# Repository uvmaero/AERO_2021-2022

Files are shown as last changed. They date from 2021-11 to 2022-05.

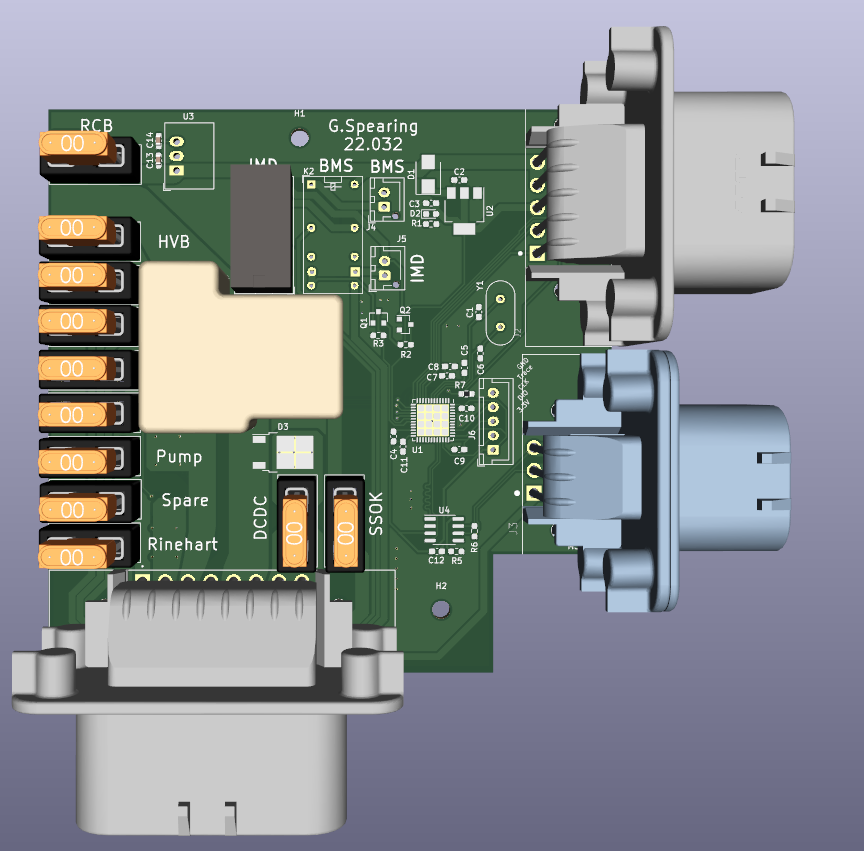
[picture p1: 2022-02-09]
Board_Images/RCB_3d_front.png

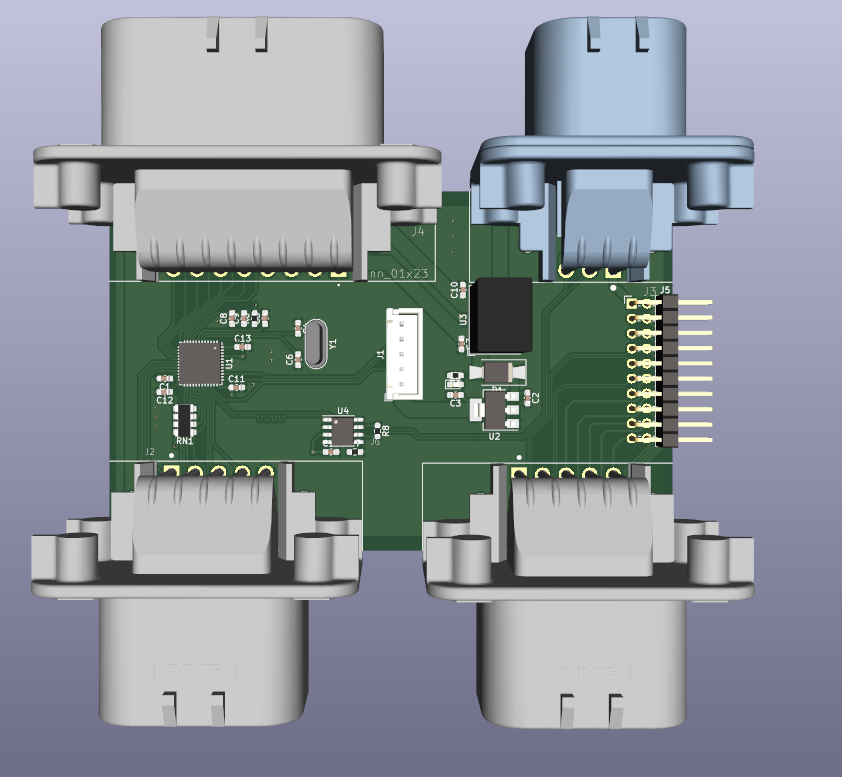
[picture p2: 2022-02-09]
Board_Images/DCB_3d_front.png

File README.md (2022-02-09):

# AERO_2021-2022

AERO Code and PCBs for CleanSpeed 5.0

This is all the boards and code we generate

## File Structure
Files here are for both the PCB and the firmware. 

{Board_Name}/{Board_Name_Firmware} -> holds the files for the firmware

{Board_Name}/{Board_Name_PCB} -> holds the KiCad files for the PCB

## Board Information

 - BCP: BMS Connector Pass through
 - DCB: Driver Contorl Board
 - HVB: High Voltage Board
 - MRP: Motor Resolver Passthrough
 - RCB: Rear Control Board

To read more about the boards go to [Board Descriptions](Board_Descriptions.md)

## Code Information

Code descrpitions can be found in [Firmware Descriptions](Firmware_Descriptions.md)

## Wireless Transceiver Information

There's also a wireless project. More information to come.

## Willem Review Notes: 

@Willem -> put any notes you have regarding boards here. 
Please review RCB, DCB, HVB, PAM

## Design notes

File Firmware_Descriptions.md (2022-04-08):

# Firmware Descrptions

Here you'll find more information about the firmware of each of the boards throughout the car. You can expect to find documentation for things like each function used, a program flow chart, CAN addresses and message content, and more. 

## Diver Control Board
### Overview: 
This board controls all of the hardware that the driver needs to interface with to drive the car, as well as gathers sensor data from the forward sensors. For the driver, this board manages the LCD heads up display and each of the controls that modifies the way the car drives. The coast regeneration and brake regeneration knobs, start button, accelerate and brake pedals all send their data to the Driver Control Board. The HUD that provides information to the driver about the is driven by this board as well. Like all boards on the car, this board communicates with the rest of the vehicle using the CAN protocol. 
### Flowchart:

### Function Definitons:
#### pollSensorData:
Input Parameters: void  
Return Type & Value: void  
Description: Reads each sensor that the board monitors and updates the appropriate global variable holding the sensor value.  
### HAL_GPIO_EXTI_Callback
Input Parameters: uint16_t GPIO_PIN
Return Type & Value: void
Description: The IRQ handler for the start button, this will send a ready to drive CAN message to rinehart, enabling the car to drive!

### accel_pedal_compare
Input Parameters: uint8_t pedal0, uint8_t pedal1
Return Type & Value: uint8_t pedal_average (the average pedal value computed)
Description: compares the two samples from the pedal potentiometeres to ensure that the values are within 10 millivolts of eachother to prevent unintended acceleration (very dangerous!)

### CAN Information: 
#### Outgoing Messages:
Front Left Wheel Speed: int 0 - 255 (rpm)  
Front Right Wheel Speed: int 0 - 255  
Front Right Suspension: int 0 - 255 (spring depression scaled to 0 - 255)  
Front Left Suspension: int 0 - 255 (spring depression scaled to 0 - 255)  
Brake 1: 
Brake 2: 
Pedal 1: 
Pedal 2: 

#### Incoming Messages:
Rear Left Wheel Speed: Rear Control Board - int 0 - 255 (rpm)  
Rear Right Wheel Speed: Rear Control Board - int 0 - 255 (rpm)  
Rear Right Suspension: Rear Control Board - int 0 - 255 (spring depression scaled to 0 - 255)  
Rear Left Suspension: Rear Control Board - int 0 - 255 (spring depression scaled to 0 - 255)  
Read to Drive State: High Voltage Board - int 0 or 1 

#### Addresses:
0x90: Base - [0x00, 0x01, 0x02, 0x03, 0x04, 0x05, 0x06, 0x07]  
0x91: Prog - [Torque Setting, 0x01, 0x02, 0x03, 0x04, 0x05, 0x06, 0x07]  
0x92: DAQ-DATA - [Left Wheel Speed, Right Wheel Speed, Left Suspension, Right Suspension, Brake 1, Brake 2, Pedal 1, Pedal 2]    
0x93: CONTROL DATA - [Brake Regen, Coast Regen, Cooling, Drive Direction, 0x04, 0x05, 0x06, 0x07]  

## Rear Control Board
### Overview: 
### Flowchart:

### Function Definitons:
#### pollSensorData:
Input Parameters: void  
Return Type & Value: void  
Description: Reads each sensor that the board monitors and updates the appropriate global variable holding the sensor value.

### CAN Information: 

#### Outgoing Messages:
Rear Left Wheel Speed: int 0 - 255 (rpm)  
Rear Right Wheel Speed: int 0 - 255  
Rear Right Suspension: int 0 - 255 (spring depression scaled to 0 - 255)  
Rear Left Suspension: int 0 - 255 (spring depression scaled to 0 - 255)  

#### Incoming Messages:
Brake Light State: Dash Control Board - int 0 or 1
Fan State: Dash Control Board - int 0 or 1

#### Addresses:
0x80: Base - [0x00, 0x01, 0x02, 0x03, 0x04, 0x05, 0x06, 0x07]  
0x81: DAQ DATA - [Left Wheel Speed, Right Wheel Speed, Left Suspension, Right Suspension, Water Temperature Inlet, Water Temperature Outlet, 0x06, 0x07]  
0x82: CONTROL DATA - [Brake Signal, Pump Signal, Fan Signal, 0x04, 0x05, 0x06, 0x07]  

## High Voltage Board
### Overview: 
### Flowchart:

### Function Definitons:
#### pollSensorData:
Input Parameters: void  
Return Type & Value: void  
Description: Reads each sensor that the board monitors and updates the appropriate global variable holding the sensor value.

### CAN Information:

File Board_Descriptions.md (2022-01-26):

# Board Descirptions

This file will list the boards and where to find more information about them. 

## Diver Control Board

## Driver Interface Board

## Rear Control Board

## High Voltage Board

## Pack Manager Board

## Emrax Resolver Board

## BMS Pass Through Board

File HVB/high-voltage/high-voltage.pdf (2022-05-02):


12/04/2022

high-voltage Project
Configuration Report

## 1. Description

### 1.1. Project

Project Name | high-voltage
Board Name | custom
Generated with: | STM32CubeMX 6.4.0
Date | 04/12/2022

### 1.2. MCU

MCU Series | STM32F4
MCU Line | STM32F413/423
MCU name | STM32F413CGUx
MCU Package | UFQFPN48
MCU Pin number | 48

### 1.3. Core(s) information

Core(s) | Arm Cortex-M4

## 2. Pinout Configuration

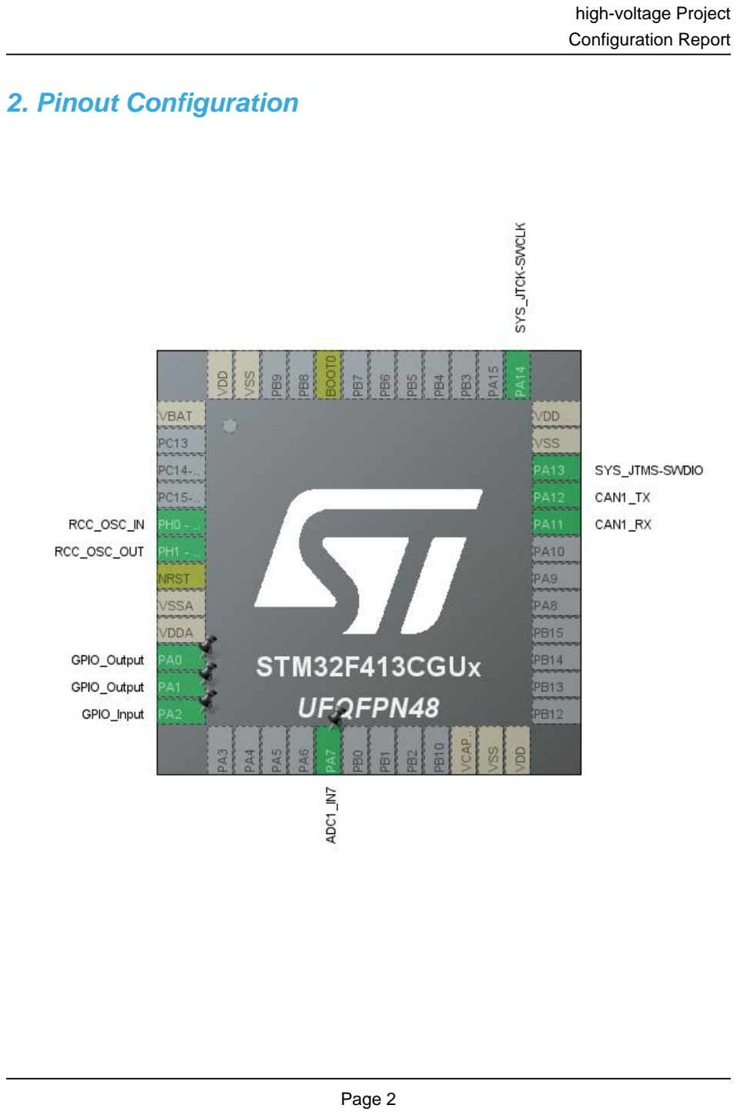
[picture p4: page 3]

## 3. Pins Configuration

Pin Number UFQFPN48 | Pin Name (function after reset) | Pin Type | Alternate Function(s) | Label
1 | VBAT | Power
5 | PH0 - OSC_IN | I/O | RCC_OSC_IN
6 | PH1 - OSC_OUT | I/O | RCC_OSC_OUT
7 | NRST | Reset
8 | VSSA | Power
9 | VDDA | Power
10 | PA0 * | I/O | GPIO_Output
11 | PA1 * | I/O | GPIO_Output
12 | PA2 * | I/O | GPIO_Input
17 | PA7 | I/O | ADC1_IN7
22 | VCAP_1 | Power
23 | VSS | Power
24 | VDD | Power
32 | PA11 | I/O | CAN1_RX
33 | PA12 | I/O | CAN1_TX
34 | PA13 | I/O | SYS_JTMS-SWDIO
35 | VSS | Power
36 | VDD | Power
37 | PA14 | I/O | SYS_JTCK-SWCLK
44 | BOOT0 | Boot
47 | VSS | Power
48 | VDD | Power

* The pin is affected with an I/O function

## 4. Clock Tree Configuration

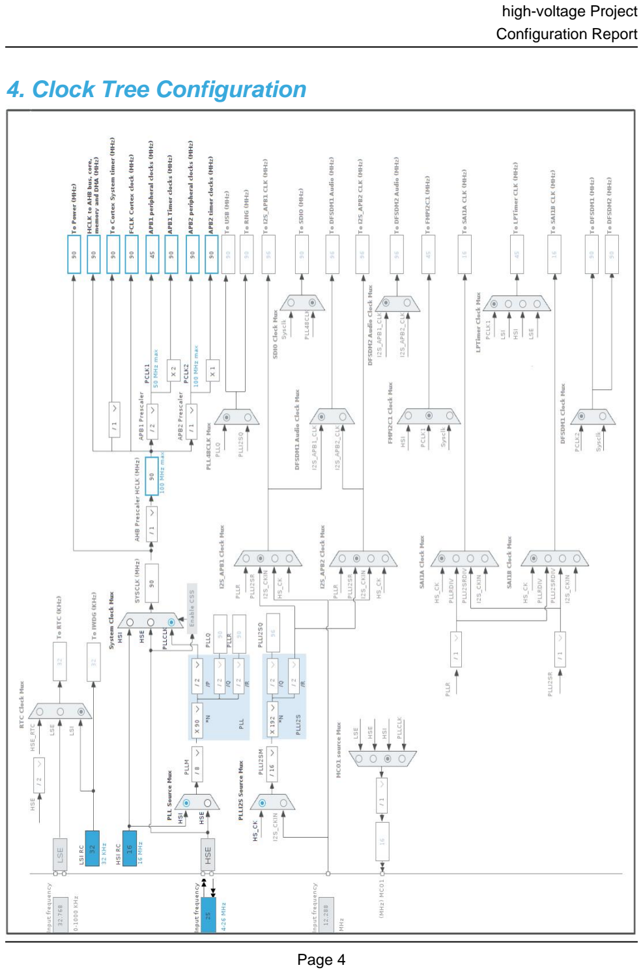
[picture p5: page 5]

## 5. Software Project

### 5.1. Project Settings

Name | Value
Project Name | high-voltage
Project Folder | /home/george/Documents/GitHub/AERO/AERO_2021-2022/HVB/high-voltage
Toolchain / IDE | Makefile
Firmware Package Name and Version | STM32Cube FW_F4 V1.26.2
Application Structure | Advanced
Generate Under Root | No
Do not generate the main() | No
Minimum Heap Size | 0x200
Minimum Stack Size | 0x400

### 5.2. Code Generation Settings

Name | Value
STM32Cube MCU packages and embedded software | Copy only the necessary library files
Generate peripheral initialization as a pair of '.c/.h' files | No
Backup previously generated files when re-generating | No
Keep User Code when re-generating | Yes
Delete previously generated files when not re-generated | Yes
Set all free pins as analog (to optimize the power consumption) | No
Enable Full Assert | No

### 5.3. Advanced Settings - Generated Function Calls

Rank | Function Name | Peripheral Instance Name
1 | MX_GPIO_Init | GPIO
2 | SystemClock_Config | RCC
3 | MX_CAN1_Init | CAN1
4 | MX_DMA_Init | DMA
5 | MX_ADC1_Init | ADC1
6 | MX_TIM14_Init | TIM14
7 | MX_TIM13_Init | TIM13

## 6. Power Consumption Calculator report

### 6.1. Microcontroller Selection

Series | STM32F4
Line | STM32F413/423
MCU | STM32F413CGUx
Datasheet | DS11581_Rev5

### 6.2. Parameter Selection

Temperature | 25
Vdd | 1.7

### 6.3. Battery Selection

Battery | Li-SOCL2(A3400)
Capacity | 3400.0 mAh
Self Discharge | 0.08 %/month
Nominal Voltage | 3.6 V
Max Cont Current | 100.0 mA
Max Pulse Current | 200.0 mA
Cells in series | 1
Cells in parallel | 1

### 6.4. Sequence

Step | Step1 | Step2
Mode | RUN | STOP
Vdd | 1.7 | 1.7
Voltage Source | Battery | Battery
Range | Scale1-High | No Scale
Fetch Type | FLASH/ART/PREFETCH | n/a
CPU Frequency | 100 MHz | 0 Hz
Clock Configuration | HSE PLL | Regulator_LPLV Flash-PwrDwn
Clock Source Frequency | 4 MHz | 0 Hz
Peripherals
Additional Cons. | 0 mA | 0 mA
Average Current | 25.4 mA | 15.3 µA
Duration | 0.1 ms | 0.9 ms
DMIPS | 125.0 | 0.0
Ta Max | 103.62 | 105
Category | In DS Table | In DS Table

### 6.5. Results

Sequence Time | 1 ms | Average Current | 2.55 mA
Battery Life | 1 month, 24 days, 23 hours | Average DMIPS | 125.0 DMIPS

### 6.6. Chart

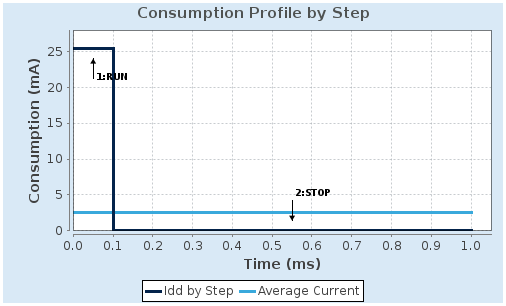
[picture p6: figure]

## 7. Peripherals and Middlewares Configuration

### 7.1. ADC1

mode: IN7
7.1.1. Parameter Settings:

ADCs_Common_Settings:

Mode | Independent mode
ADC_Settings:
Clock Prescaler | PCLK2 divided by 4
Resolution | 12 bits (15 ADC Clock cycles)
Data Alignment | Right alignment
Scan Conversion Mode | Disabled
Continuous Conversion Mode | Enabled *
Discontinuous Conversion Mode | Disabled
DMA Continuous Requests | Enabled *
End Of Conversion Selection | EOC flag at the end of single channel conversion
ADC_Regular_ConversionMode:
Number Of Conversion | 1
External Trigger Conversion Source | Regular Conversion launched by software
External Trigger Conversion Edge | None
Rank | 1
Channel | Channel 7
Sampling Time | 3 Cycles
ADC_Injected_ConversionMode:
Number Of Conversions | 0
WatchDog:
Enable Analog WatchDog Mode | false

### 7.2. CAN1

mode: Activated
7.2.1. Parameter Settings:

Bit Timings Parameters:

Prescaler (for Time Quantum) | 6 *
Time Quantum | 133.33333333333331 *
Time Quanta in Bit Segment 1 | 12 Times *
Time Quanta in Bit Segment 2 | 2 Times *

Time for one Bit | 1999 *
Baud Rate | 500000 *
ReSynchronization Jump Width | 1 Time
Basic Parameters:
Time Triggered Communication Mode | Disable
Automatic Bus-Off Management | Enable *
Automatic Wake-Up Mode | Enable *
Automatic Retransmission | Enable *
Receive Fifo Locked Mode | Disable
Transmit Fifo Priority | Disable
Advanced Parameters:
Operating Mode | Normal

### 7.3. RCC

High Speed Clock (HSE): Crystal/Ceramic Resonator
7.3.1. Parameter Settings:

System Parameters:

VDD voltage (V) | 3.3
Instruction Cache | Enabled
Prefetch Buffer | Enabled
Data Cache | Enabled
Flash Latency(WS) | 3 WS (4 CPU cycle)
RCC Parameters:
HSI Calibration Value | 16
TIM Prescaler Selection | Disabled
HSE Startup Timout Value (ms) | 100
LSE Startup Timout Value (ms) | 5000
Power Parameters:
Power Regulator Voltage Scale | Power Regulator Voltage Scale 1

### 7.4. SYS

Debug: Serial Wire
Timebase Source: SysTick

### 7.5. TIM13

mode: Activated
7.5.1. Parameter Settings:

Counter Settings:

Prescaler (PSC - 16 bits value) | 9000-1 *
Counter Mode | Up
Counter Period (AutoReload Register - 16 bits value ) | 1000-1 *
Internal Clock Division (CKD) | No Division
auto-reload preload | Disable

### 7.6. TIM14

mode: Activated
7.6.1. Parameter Settings:

Counter Settings:

Prescaler (PSC - 16 bits value) | 9000-1 *
Counter Mode | Up
Counter Period (AutoReload Register - 16 bits value ) | 5000-1 *
Internal Clock Division (CKD) | No Division
auto-reload preload | Disable

* User modified value

## 8. System Configuration

### 8.1. GPIO configuration

IP | Pin | Signal | GPIO mode | GPIO pull/up pull down | Max Speed | User Label
ADC1 | PA7 | ADC1_IN7 | Analog mode | No pull-up and no pull-down | n/a
CAN1 | PA11 | CAN1_RX | Alternate Function Push Pull | No pull-up and no pull-down | High *
| PA12 | CAN1_TX | Alternate Function Push Pull | No pull-up and no pull-down | High *
RCC | PH0 -OSC_IN | RCC_OSC_IN | n/a | n/a | n/a
| PH1 -OSC_OUT | RCC_OSC_OUT | n/a | n/a | n/a
SYS | PA13 | SYS_JTMS-SWDIO | n/a | n/a | n/a
| PA14 | SYS_JTCK-SWCLK | n/a | n/a | n/a
GPIO | PA0 | GPIO_Output | Output Push Pull | Pull-down * | Low
| PA1 | GPIO_Output | Output Push Pull | Pull-up * | Low
| PA2 | GPIO_Input | Input mode | No pull-up and no pull-down | n/a

### 8.2. DMA configuration

DMA request | Stream | Direction | Priority
ADC1 | DMA2_Stream0 | Peripheral To Memory | Low

ADC1: DMA2_Stream0 DMA request Settings:

Mode: | Circular *
Use fifo: | Disable
Peripheral Increment: | Disable
Memory Increment: | Enable *
Peripheral Data Width: | Half Word
Memory Data Width: | Half Word

### 8.3. NVIC configuration

8.3.1. NVIC
Interrupt Table | Enable | Preenmption Priority | SubPriority
Non maskable interrupt | true | 0 | 0
Hard fault interrupt | true | 0 | 0
Memory management fault | true | 0 | 0
Pre-fetch fault, memory access fault | true | 0 | 0
Undefined instruction or illegal state | true | 0 | 0
System service call via SWI instruction | true | 0 | 0
Debug monitor | true | 0 | 0
Pendable request for system service | true | 0 | 0
System tick timer | true | 15 | 0
CAN1 RX0 interrupts | true | 0 | 0
TIM8 update interrupt and TIM13 global interrupt | true | 0 | 0
TIM8 trigger and commutation interrupts and TIM14 global interrupt | true | 0 | 0
DMA2 stream0 global interrupt | true | 0 | 0
PVD interrupt through EXTI line 16 | | unused
Flash global interrupt | | unused
RCC global interrupt | | unused
ADC1 global interrupt | | unused
CAN1 TX interrupts | | unused
CAN1 RX1 interrupt | | unused
CAN1 SCE interrupt | | unused
FPU global interrupt | | unused
8.3.2. NVIC Code generation

Enabled interrupt Table Select for init
sequence ordering
| | Generate IRQ
| | handler | Call HAL handler
Non maskable interrupt | false | true | false
Hard fault interrupt | false | true | false
Memory management fault | false | true | false
Pre-fetch fault, memory access fault | false | true | false
Undefined instruction or illegal state | false | true | false
System service call via SWI instruction | false | true | false
Debug monitor | false | true | false
Pendable request for system service | false | true | false
System tick timer | false | true | true
CAN1 RX0 interrupts | false | true | true

Enabled interrupt Table | Select for init sequence ordering | Generate IRQ handler | Call HAL handler
TIM8 update interrupt and TIM13 global interrupt | false | true | true
TIM8 trigger and commutation interrupts and TIM14 global interrupt | false | true | true
DMA2 stream0 global interrupt | false | true | true

* User modified value

## 9. System Views

9.1. Category view
9.1.1. Current

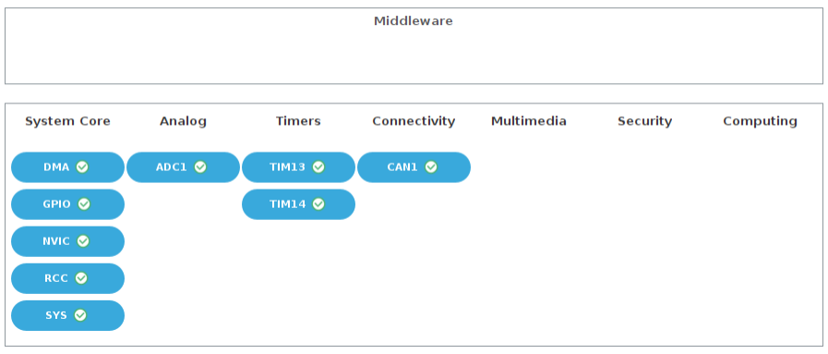
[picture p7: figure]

## 10. Docs & Resources

Type | Link
Datasheet | http://www.st.com/resource/en/datasheet/DM00282249.pdf
Reference manual | http://www.st.com/resource/en/reference_manual/DM00305666.pdf
Programming manual | http://www.st.com/resource/en/programming_manual/DM00046982.pdf
Errata sheet | http://www.st.com/resource/en/errata_sheet/DM00318678.pdf
Application note | http://www.st.com/resource/en/application_note/CD00167594.pdf
Application note | http://www.st.com/resource/en/application_note/CD00211314.pdf
Application note | http://www.st.com/resource/en/application_note/CD00249778.pdf
Application note | http://www.st.com/resource/en/application_note/CD00259245.pdf
Application note | http://www.st.com/resource/en/application_note/CD00264321.pdf
Application note | http://www.st.com/resource/en/application_note/CD00264342.pdf
Application note | http://www.st.com/resource/en/application_note/CD00264379.pdf
Application note | http://www.st.com/resource/en/application_note/DM00024853.pdf
Application note | http://www.st.com/resource/en/application_note/DM00040802.pdf
Application note | http://www.st.com/resource/en/application_note/DM00040808.pdf
Application note | http://www.st.com/resource/en/application_note/DM00042534.pdf
Application note | http://www.st.com/resource/en/application_note/DM00046011.pdf
Application note | http://www.st.com/resource/en/application_note/DM00072315.pdf
Application note | http://www.st.com/resource/en/application_note/DM00073742.pdf
Application note | http://www.st.com/resource/en/application_note/DM00073853.pdf
Application note | http://www.st.com/resource/en/application_note/DM00080497.pdf
Application note | http://www.st.com/resource/en/application_note/DM00081379.pdf
Application note | http://www.st.com/resource/en/application_note/DM00115714.pdf
Application note | http://www.st.com/resource/en/application_note/DM00129215.pdf
Application note | http://www.st.com/resource/en/application_note/DM00160482.pdf
Application note | http://www.st.com/resource/en/application_note/DM00213525.pdf

Application note | http://www.st.com/resource/en/application_note/DM00220769.pdf
Application note | http://www.st.com/resource/en/application_note/DM00226326.pdf
Application note | http://www.st.com/resource/en/application_note/DM00227538.pdf
Application note | http://www.st.com/resource/en/application_note/DM00236305.pdf
Application note | http://www.st.com/resource/en/application_note/DM00257177.pdf
Application note | http://www.st.com/resource/en/application_note/DM00272912.pdf
Application note | http://www.st.com/resource/en/application_note/DM00281138.pdf
Application note | http://www.st.com/resource/en/application_note/DM00296349.pdf
Application note | http://www.st.com/resource/en/application_note/DM00315319.pdf
Application note | http://www.st.com/resource/en/application_note/DM00325582.pdf
Application note | http://www.st.com/resource/en/application_note/DM00327191.pdf
Application note | http://www.st.com/resource/en/application_note/DM00343623.pdf
Application note | http://www.st.com/resource/en/application_note/DM00354244.pdf
Application note | http://www.st.com/resource/en/application_note/DM00354333.pdf
Application note | http://www.st.com/resource/en/application_note/DM00377852.pdf
Application note | http://www.st.com/resource/en/application_note/DM00380469.pdf
Application note | http://www.st.com/resource/en/application_note/DM00395696.pdf
Application note | http://www.st.com/resource/en/application_note/DM00431633.pdf
Application note | http://www.st.com/resource/en/application_note/DM00493651.pdf
Application note | http://www.st.com/resource/en/application_note/DM00536349.pdf
Application note | http://www.st.com/resource/en/application_note/DM00725181.pdf

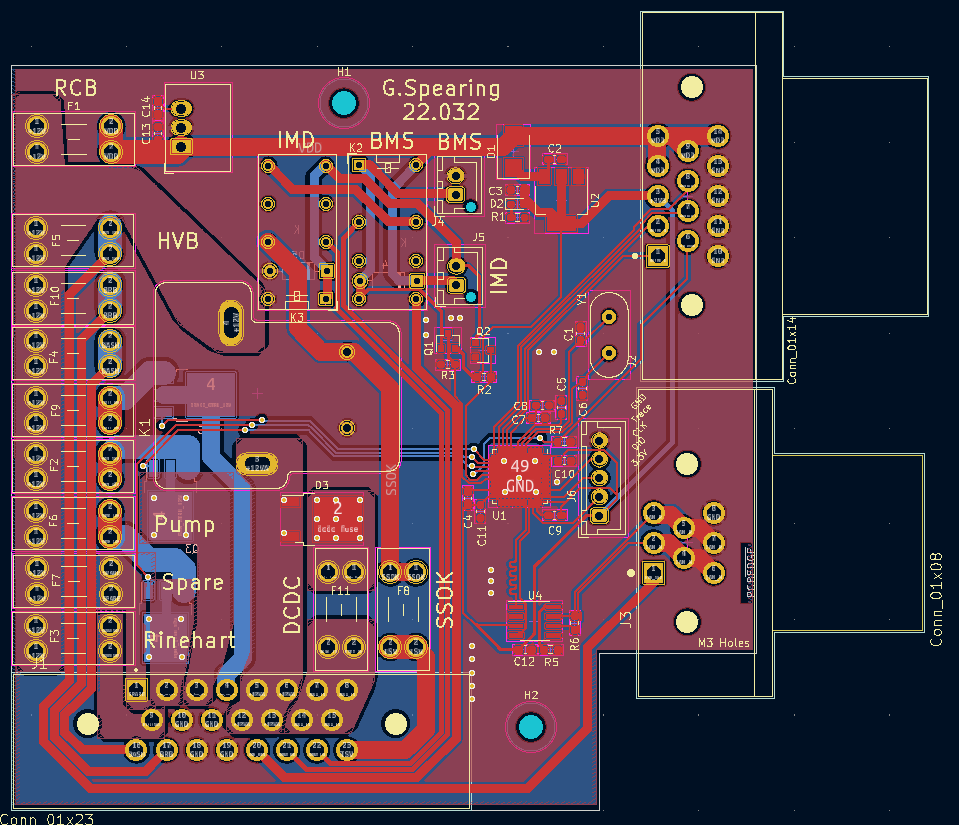
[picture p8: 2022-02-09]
Board_Images/RCB_front.png

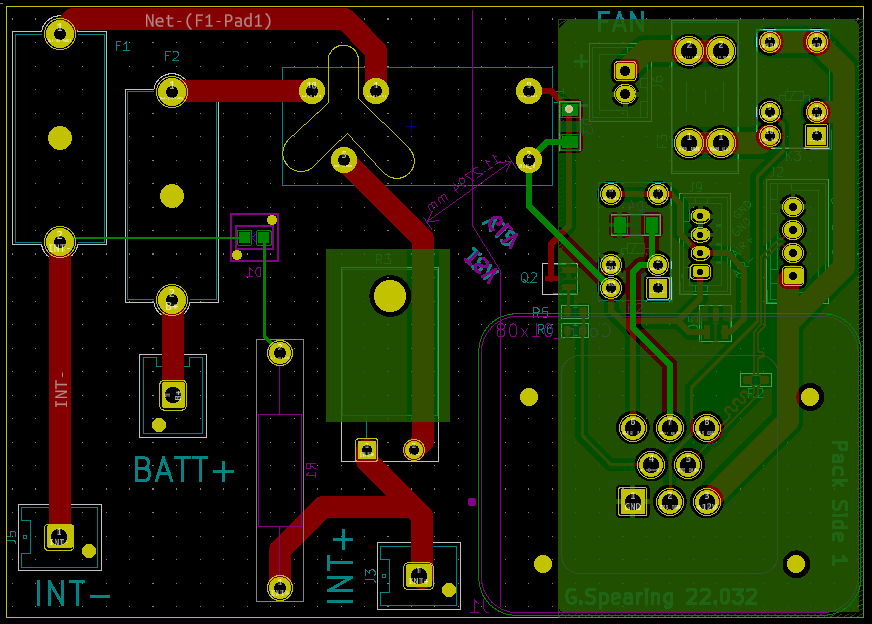
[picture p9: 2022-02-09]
Board_Images/Pacman1_back.png

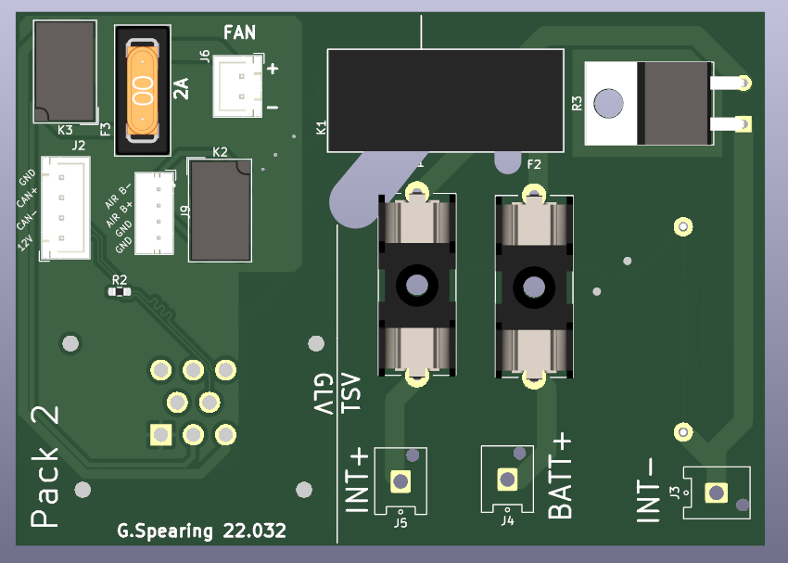
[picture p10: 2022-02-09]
Board_Images/Pacman2_3d_front.png

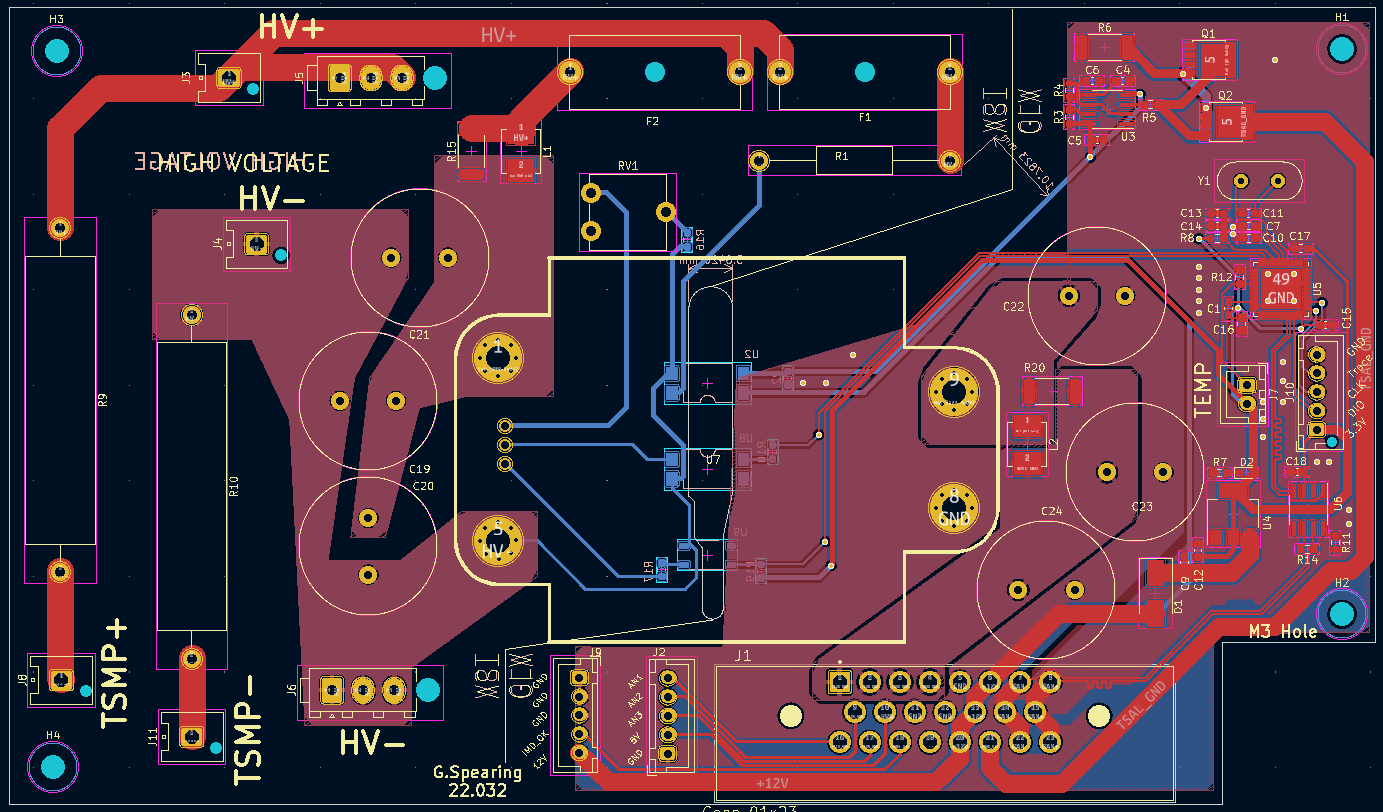
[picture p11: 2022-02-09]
Board_Images/HVB_front.png

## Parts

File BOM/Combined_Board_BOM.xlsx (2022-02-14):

Notes | Board | Ref | Value | Footprint | Datasheet | Manufacturer | Vendor
In Stock | DCB | C1 | .1u | Capacitor_SMD:C_0603_1608Metric_Pad1.08x0.95mm_HandSolder | ~
In Stock | HVB | C1 | 4.7u | Capacitor_SMD:C_0603_1608Metric_Pad1.08x0.95mm_HandSolder | ~
In Stock | RCB | C1 | .1u | Capacitor_SMD:C_0603_1608Metric_Pad1.08x0.95mm_HandSolder | ~
In Stock | DEMO | C10 | 0.1u | Capacitor_SMD:C_0603_1608Metric_Pad1.08x0.95mm_HandSolder | ~
In Stock | DCB | C10 | 0.1u | Capacitor_SMD:C_0603_1608Metric_Pad1.08x0.95mm_HandSolder | ~
In Stock | HVB | C10 | 0.1u | Capacitor_SMD:C_0603_1608Metric_Pad1.08x0.95mm_HandSolder | ~
In Stock | RCB | C10 | 0.1u | Capacitor_SMD:C_0603_1608Metric_Pad1.08x0.95mm_HandSolder | ~
In Stock | DEMO | C11 | 0.1u | Capacitor_SMD:C_0603_1608Metric_Pad1.08x0.95mm_HandSolder | ~
In Stock | DCB | C11 | 0.1u | Capacitor_SMD:C_0603_1608Metric_Pad1.08x0.95mm_HandSolder | ~
In Stock | RCB | C11 | 0.1u | Capacitor_SMD:C_0603_1608Metric_Pad1.08x0.95mm_HandSolder | ~
In Stock | DEMO | C12 | 0.1u | Capacitor_SMD:C_0603_1608Metric_Pad1.08x0.95mm_HandSolder | ~
In Stock | DCB | C12 | 0.1u | Capacitor_SMD:C_0603_1608Metric_Pad1.08x0.95mm_HandSolder | ~
In Stock | HVB | C12 | 10u | Capacitor_SMD:C_0603_1608Metric_Pad1.08x0.95mm_HandSolder | ~
In Stock | RCB | C12 | 0.1u | Capacitor_SMD:C_0603_1608Metric_Pad1.08x0.95mm_HandSolder | ~
In Stock | HVB | C13 | 0.1u | Capacitor_SMD:C_0603_1608Metric_Pad1.08x0.95mm_HandSolder | ~
In Stock | RCB | C13 | 1u | Capacitor_SMD:C_0603_1608Metric_Pad1.08x0.95mm_HandSolder | ~
In Stock | HVB | C15 | 0.1u | Capacitor_SMD:C_0603_1608Metric_Pad1.08x0.95mm_HandSolder | ~
In Stock | HVB | C16 | 0.1u | Capacitor_SMD:C_0603_1608Metric_Pad1.08x0.95mm_HandSolder | ~
In Stock | HVB | C17 | 0.1u | Capacitor_SMD:C_0603_1608Metric_Pad1.08x0.95mm_HandSolder | ~
In Stock | HVB | C19 | 0.68uF | Capacitor_THT:C_Rect_L18.0mm_W8.0mm_P15.00mm_FKS3_FKP3 | ~
In Stock | DEMO | C2 | .1u | Capacitor_SMD:C_0603_1608Metric_Pad1.08x0.95mm_HandSolder | ~
In Stock | HVB | C2 | 0.68uF | Capacitor_THT:C_Rect_L18.0mm_W8.0mm_P15.00mm_FKS3_FKP3 | ~
In Stock | RCB | C2 | 1u | Capacitor_SMD:C_0603_1608Metric_Pad1.08x0.95mm_HandSolder | ~
In Stock | HVB | C22 | 4700uF | Capacitor_THT:C_Radial_D18.0mm_H35.5mm_P7.50mm | ~
In Stock | HVB | C23 | 4700uF | Capacitor_THT:C_Radial_D18.0mm_H35.5mm_P7.50mm | ~
In Stock | DEMO | C3 | 10u | Capacitor_SMD:C_0603_1608Metric_Pad1.08x0.95mm_HandSolder | ~
In Stock | HVB | C3 | 0.1u | Capacitor_SMD:C_0603_1608Metric_Pad1.08x0.95mm_HandSolder | ~
In Stock | RCB | C3 | 1u | Capacitor_SMD:C_0603_1608Metric_Pad1.08x0.95mm_HandSolder | ~
In Stock | DEMO | C4 | 4.7u | Capacitor_SMD:C_0603_1608Metric_Pad1.08x0.95mm_HandSolder | ~
In Stock | DCB | C4 | 4.7u | Capacitor_SMD:C_0603_1608Metric_Pad1.08x0.95mm_HandSolder | ~
In Stock | HVB | C4 | 0.1u | Capacitor_SMD:C_0603_1608Metric_Pad1.08x0.95mm_HandSolder | ~
In Stock | RCB | C4 | 4.7u | Capacitor_SMD:C_0603_1608Metric_Pad1.08x0.95mm_HandSolder | ~
In Stock | DEMO | C5 | 0.1u | Capacitor_SMD:C_0603_1608Metric_Pad1.08x0.95mm_HandSolder | ~
In Stock | DCB | C5 | 0.1u | Capacitor_SMD:C_0603_1608Metric_Pad1.08x0.95mm_HandSolder | ~
In Stock | HVB | C5 | 0.1u | Capacitor_SMD:C_0603_1608Metric_Pad1.08x0.95mm_HandSolder | ~
In Stock | RCB | C5 | 0.1u | Capacitor_SMD:C_0603_1608Metric_Pad1.08x0.95mm_HandSolder | ~
In Stock | DCB | C6 | 10u | Capacitor_SMD:C_0603_1608Metric_Pad1.08x0.95mm_HandSolder | ~
In Stock | HVB | C6 | 1u | Capacitor_SMD:C_0603_1608Metric_Pad1.08x0.95mm_HandSolder | ~
In Stock | RCB | C6 | 10u | Capacitor_SMD:C_0603_1608Metric_Pad1.08x0.95mm_HandSolder | ~
In Stock | DEMO | C7 | 0.1u | Capacitor_SMD:C_0603_1608Metric_Pad1.08x0.95mm_HandSolder | ~
In Stock | DCB | C7 | 0.1u | Capacitor_SMD:C_0603_1608Metric_Pad1.08x0.95mm_HandSolder | ~
In Stock | HVB | C7 | 0.1u | Capacitor_SMD:C_0603_1608Metric_Pad1.08x0.95mm_HandSolder | ~
In Stock | RCB | C7 | 0.1u | Capacitor_SMD:C_0603_1608Metric_Pad1.08x0.95mm_HandSolder | ~
In Stock | DEMO | C8 | 0.1u | Capacitor_SMD:C_0603_1608Metric_Pad1.08x0.95mm_HandSolder | ~
In Stock | DCB | C8 | 0.1u | Capacitor_SMD:C_0603_1608Metric_Pad1.08x0.95mm_HandSolder | ~
In Stock | RCB | C8 | 0.1u | Capacitor_SMD:C_0603_1608Metric_Pad1.08x0.95mm_HandSolder | ~
In Stock | DEMO | C9 | 0.1u | Capacitor_SMD:C_0603_1608Metric_Pad1.08x0.95mm_HandSolder | ~
In Stock | DCB | C9 | 0.1u | Capacitor_SMD:C_0603_1608Metric_Pad1.08x0.95mm_HandSolder | ~
In Stock | HVB | C9 | .1u | Capacitor_SMD:C_0603_1608Metric_Pad1.08x0.95mm_HandSolder | ~
In Stock | RCB | C9 | 0.1u | Capacitor_SMD:C_0603_1608Metric_Pad1.08x0.95mm_HandSolder | ~
In Stock | DEMO | D1 | LED | LED_SMD:LED_0603_1608Metric_Pad1.05x0.95mm_HandSolder | ~
In Stock | DCB | D1 | LED | LED_SMD:LED_0603_1608Metric_Pad1.05x0.95mm_HandSolder | ~
In Stock | HVB | D1 | BAT54GW | Diode_SMD:D_SOD-123 | ~
In Stock | Pacman | D1 | LED | AERO_Footprints:LPA-C011301S-x LED 0805 LIGHT PIPE SINGLE VERT SMD | ~
In Stock | Pacman | D1 | LED | AERO_Footprints:LPA-C011301S-x LED 0805 LIGHT PIPE SINGLE VERT SMD | ~
In Stock | RCB | D1 | LED | LED_SMD:LED_0603_1608Metric_Pad1.05x0.95mm_HandSolder | ~
In Stock | DEMO | D2 | LED | LED_SMD:LED_0603_1608Metric_Pad1.05x0.95mm_HandSolder | ~
In Stock | DCB | D2 | SP0502BAHT | Package_TO_SOT_SMD:SOT-23 | http://www.littelfuse.com/~/media/files/littelfuse/technical%20resources/documents/data%20sheets/sp05xxba.pdf
In Stock | HVB | D2 | LED | LED_SMD:LED_0603_1608Metric_Pad1.05x0.95mm_HandSolder | ~
In Stock | DCB | D3 | SP0502BAHT | Package_TO_SOT_SMD:SOT-23 | http://www.littelfuse.com/~/media/files/littelfuse/technical%20resources/documents/data%20sheets/sp05xxba.pdf
In Stock | HVB | D3 | SP0502BAHT | Package_TO_SOT_SMD:SOT-23 | http://www.littelfuse.com/~/media/files/littelfuse/technical%20resources/documents/data%20sheets/sp05xxba.pdf
In Stock | Pacman | D3 | 1N4148 | Diode_SMD:D_MiniMELF | http://www.nxp.com/documents/data_sheet/1N4148_1N4448.pdf
In Stock | Pacman | D3 | 1N4148 | Diode_SMD:D_MiniMELF | http://www.nxp.com/documents/data_sheet/1N4148_1N4448.pdf
 | RCB | D3 | D_KAK | Package_TO_SOT_SMD:TO-252-2 | ~
In Stock | DCB | D4 | SP0502BAHT | Package_TO_SOT_SMD:SOT-23 | http://www.littelfuse.com/~/media/files/littelfuse/technical%20resources/documents/data%20sheets/sp05xxba.pdf
In Stock | Pacman | D4 | 1N4148 | Diode_SMD:D_MiniMELF | http://www.nxp.com/documents/data_sheet/1N4148_1N4448.pdf
In Stock | Pacman | D4 | 1N4148 | Diode_SMD:D_MiniMELF | http://www.nxp.com/documents/data_sheet/1N4148_1N4448.pdf
In Stock | RCB | D4 | 1N4148 | Diode_SMD:D_SOD-123 | https://assets.nexperia.com/documents/data-sheet/1N4148_1N4448.pdf
In Stock | DCB | D5 | SP0502BAHT | Package_TO_SOT_SMD:SOT-23 | http://www.littelfuse.com/~/media/files/littelfuse/technical%20resources/documents/data%20sheets/sp05xxba.pdf
In Stock | Pacman | D5 | MMBZxx | Package_TO_SOT_SMD:SOT-23 | http://www.onsemi.com/pub/Collateral/MMBZ5V6ALT1-D.PDF
In Stock | Pacman | D5 | MMBZxx | Package_TO_SOT_SMD:SOT-23 | http://www.onsemi.com/pub/Collateral/MMBZ5V6ALT1-D.PDF
In Stock | RCB | D5 | 1N4148 | Diode_SMD:D_SOD-123 | https://assets.nexperia.com/documents/data-sheet/1N4148_1N4448.pdf
In Stock | DCB | D6 | SP0502BAHT | Package_TO_SOT_SMD:SOT-23 | http://www.littelfuse.com/~/media/files/littelfuse/technical%20resources/documents/data%20sheets/sp05xxba.pdf
In Stock | RCB | D6 | SP0502BAHT | Package_TO_SOT_SMD:SOT-23 | http://www.littelfuse.com/~/media/files/littelfuse/technical%20resources/documents/data%20sheets/sp05xxba.pdf
In Stock | RCB | D7 | SP0502BAHT | Package_TO_SOT_SMD:SOT-23 | http://www.littelfuse.com/~/media/files/littelfuse/technical%20resources/documents/data%20sheets/sp05xxba.pdf
In Stock | RCB | D8 | SP0502BAHT | Package_TO_SOT_SMD:SOT-23 | http://www.littelfuse.com/~/media/files/littelfuse/technical%20resources/documents/data%20sheets/sp05xxba.pdf
Order | DEMO | D9 | DESD2CAN2SOQ-7 | Package_TO_SOT_SMD:SOT-23 | http://www.onsemi.com/pub_link/Collateral/NUP2105L-D.PDF
Order | DCB | D9 | DESD2CAN2SOQ-7 | Package_TO_SOT_SMD:SOT-23 | http://www.onsemi.com/pub_link/Collateral/NUP2105L-D.PDF
Order | RCB | D9 | DESD2CAN2SOQ-7 | Package_TO_SOT_SMD:SOT-23 | http://www.onsemi.com/pub_link/Collateral/NUP2105L-D.PDF
In Stock | HVB | F1 | 2A | Fuse:Fuseholder_Cylinder-5x20mm_Schurter_0031_8201_Horizontal_Open | ~
In Stock | Pacman | F1 | 1A 300VDC | AERO_Footprints:Fuseholder_Cylinder-5x20mm_Schurter_0031_8201_Horizontal_Open_3d | ~
In Stock | Pacman | F1 | 1A 300VDC | AERO_Footprints:Fuseholder_Cylinder-5x20mm_Schurter_0031_8201_Horizontal_Open_3d | ~
In Stock | RCB | F1 | 2A | AERO_Footprints:Fuseholder_Blade_Mini_Keystone_3568 | ~
In Stock | RCB | F10 | 2A | AERO_Footprints:Fuseholder_Blade_Mini_Keystone_3568 | ~
In Stock | RCB | F11 | 20A | AERO_Footprints:Fuseholder_Blade_Mini_Keystone_3568 | ~
In Stock | HVB | F2 | 35A | Fuse:Fuseholder_Cylinder-5x20mm_Schurter_0031_8201_Horizontal_Open | ~
In Stock | Pacman | F2 | 1A 300VDC | AERO_Footprints:Fuseholder_Cylinder-5x20mm_Schurter_0031_8201_Horizontal_Open_3d | ~
In Stock | Pacman | F2 | 1A 300VDC | AERO_Footprints:Fuseholder_Cylinder-5x20mm_Schurter_0031_8201_Horizontal_Open_3d | ~
In Stock | RCB | F2 | 10A | AERO_Footprints:Fuseholder_Blade_Mini_Keystone_3568 | ~
In Stock | Pacman | F3 | Fuse | AERO_Footprints:Fuseholder_Blade_Mini_Keystone_3568 | ~
In Stock | Pacman | F3 | Fuse | AERO_Footprints:Fuseholder_Blade_Mini_Keystone_3568 | ~
In Stock | RCB | F3 | 15A | AERO_Footprints:Fuseholder_Blade_Mini_Keystone_3568 | ~
In Stock | RCB | F4 | 2A | AERO_Footprints:Fuseholder_Blade_Mini_Keystone_3568 | ~
In Stock | RCB | F5 | 2A | AERO_Footprints:Fuseholder_Blade_Mini_Keystone_3568 | ~
In Stock | RCB | F6 | 15A | AERO_Footprints:Fuseholder_Blade_Mini_Keystone_3568 | ~
In Stock | RCB | F7 | 5A | AERO_Footprints:Fuseholder_Blade_Mini_Keystone_3568 | ~
In Stock | RCB | F8 | 2A | AERO_Footprints:Fuseholder_Blade_Mini_Keystone_3568 | ~
In Stock | RCB | F9 | 1A | AERO_Footprints:Fuseholder_Blade_Mini_Keystone_3568 | ~
DNP | HVB | H1 | MountingHole | MountingHole:MountingHole_3.2mm_M3 | ~
DNP | RCB | H1 | MountingHole | MountingHole:MountingHole_3.2mm_M3 | ~
DNP | HVB | H2 | MountingHole | MountingHole:MountingHole_3.2mm_M3 | ~
DNP | RCB | H2 | MountingHole | MountingHole:MountingHole_3.2mm_M3 | ~
DNP | HVB | H3 | MountingHole | MountingHole:MountingHole_3.2mm_M3 | ~
DNP | HVB | H4 | MountingHole | MountingHole:MountingHole_3.2mm_M3 | ~
 | EMRAX | J1 | Conn_01x08 | AERO_Footprints:TE_1-776280-1_8pin_Horizontal | ~
 | HVB | J1 | Conn_01x23 | AERO_Footprints:TE_1-770669-1_23pin_Horizontal | ~
 | Pacman | J1 | Conn_01x08 | AERO_Footprints:TE_1-776276-1_8pin_Vertical | ~
 | Pacman | J1 | Conn_01x08 | AERO_Footprints:TE_1-776276-1_8pin_Vertical | ~
 | RCB | J1 | Conn_01x23 | AERO_Footprints:TE_1-770669-1_23pin_Horizontal | ~
 | HVB | J10 | FTSH-107-01-F-DV-k | Connector_PinHeader_1.27mm:PinHeader_2x07_P1.27mm_Vertical_SMD | ~
 | HVB | J11 | HV- | Connector_Hirose:Hirose_DF63M-1P-3.96DSA_1x01_P3.96mm_Vertical | ~
 | HVB | J12 | Conn_01x02 | Connector_JST:JST_XH_B2B-XH-A_1x02_P2.50mm_Vertical | ~
 | DEMO | J2 | Conn_01x20 | Connector_PinHeader_2.54mm:PinHeader_1x20_P2.54mm_Vertical | ~
 | DCB | J2 | Conn_01x14 | AERO_Footprints:TE_1-776266-1_14pin_Horizontal | ~
 | EMRAX | J2 | Conn_01x06 | Connector_JST:JST_XH_S6B-XH-A-1_1x06_P2.50mm_Horizontal | ~
 | HVB | J2 | HECS | Connector_JST:JST_XH_B5B-XH-A_1x05_P2.50mm_Vertical | ~
 | Pacman | J2 | Conn_01x04 | Connector_JST:JST_XH_B4B-XH-A_1x04_P2.50mm_Vertical | ~
 | Pacman | J2 | Conn_01x04 | Connector_JST:JST_XH_B4B-XH-A_1x04_P2.50mm_Vertical | ~
 | RCB | J2 | Conn_01x23 | AERO_Footprints:TE_1-770669-1_23pin_Horizontal | ~
 | DEMO | J3 | Conn_01x20 | Connector_PinHeader_2.54mm:PinHeader_1x20_P2.54mm_Vertical | ~
 | DCB | J3 | Conn_01x08 | AERO_Footprints:TE_1-776280-1_8pin_Horizontal | ~
 | EMRAX | J3 | Conn_01x02 | Connector_JST:JST_XH_S2B-XH-A-1_1x02_P2.50mm_Horizontal | ~
 | HVB | J3 | HV+ | Connector_Hirose:Hirose_DF63M-1P-3.96DSA_1x01_P3.96mm_Vertical | ~
 | Pacman | J3 | Conn_01x01 | Connector_Hirose:Hirose_DF63M-1P-3.96DSA_1x01_P3.96mm_Vertical | ~
 | Pacman | J3 | Conn_01x01 | Connector_Hirose:Hirose_DF63M-1P-3.96DSA_1x01_P3.96mm_Vertical | ~
 | RCB | J3 | Conn_01x08 | AERO_Footprints:TE_1-776280-1_8pin_Horizontal | ~
 | DCB | J4 | Conn_01x23 | AERO_Footprints:TE_1-770669-1_23pin_Horizontal | ~
 | HVB | J4 | HV- | Connector_Hirose:Hirose_DF63M-1P-3.96DSA_1x01_P3.96mm_Vertical | ~
 | Pacman | J4 | Conn_01x01 | Connector_Hirose:Hirose_DF63M-1P-3.96DSA_1x01_P3.96mm_Vertical | ~
 | Pacman | J4 | Conn_01x01 | Connector_Hirose:Hirose_DF63M-1P-3.96DSA_1x01_P3.96mm_Vertical | ~
 | RCB | J4 | JST-B2B-VERT-2PIN | Connector_JST:JST_XH_B2B-XH-AM_1x02_P2.50mm_Vertical | ~
 | DCB | J5 | Conn_02x10_Counter_Clockwise | Connector_PinHeader_2.54mm:PinHeader_2x10_P2.54mm_Horizontal | ~
 | HVB | J5 | HV+ | AERO_Footprints:TE_MATE-N-LOK_1-770870-x_1x03_P4.14mm_Vertical | ~
 | Pacman | J5 | Conn_01x01 | Connector_Hirose:Hirose_DF63M-1P-3.96DSA_1x01_P3.96mm_Vertical | ~
 | Pacman | J5 | Conn_01x01 | Connector_Hirose:Hirose_DF63M-1P-3.96DSA_1x01_P3.96mm_Vertical | ~
 | RCB | J5 | JST-B2B-VERT-2PIN | Connector_JST:JST_XH_B2B-XH-AM_1x02_P2.50mm_Vertical | ~
 | DEMO | J6 | FTSH-107-01-F-DV-K | Connector_PinHeader_1.27mm:PinHeader_2x07_P1.27mm_Vertical_SMD | ~
 | DCB | J6 | Conn_01x14 | AERO_Footprints:TE_1-776266-1_14pin_Horizontal | ~
 | HVB | J6 | HV- | AERO_Footprints:TE_MATE-N-LOK_1-770870-x_1x03_P4.14mm_Vertical | ~
 | Pacman | J6 | Conn_01x02 | Connector_JST:JST_XH_B2B-XH-A_1x02_P2.50mm_Vertical | ~
 | Pacman | J6 | Conn_01x02 | Connector_JST:JST_XH_B2B-XH-A_1x02_P2.50mm_Vertical | ~
 | RCB | J6 | FTSH-107-01-F-DV-K | Connector_PinHeader_1.27mm:PinHeader_2x07_P1.27mm_Vertical_SMD | ~
 | DCB | J7 | FTSH-107-01-F-DV-K | Connector_PinHeader_1.27mm:PinHeader_2x07_P1.27mm_Vertical_SMD | ~
 | HVB | J7 | Conn_01x02 | Connector_JST:JST_XH_B2B-XH-A_1x02_P2.50mm_Vertical | ~
 | HVB | J8 | HV+ | Connector_Hirose:Hirose_DF63M-1P-3.96DSA_1x01_P3.96mm_Vertical | ~
 | HVB | J9 | Bender-LV | Connector_JST:JST_XH_B5B-XH-A_1x05_P2.50mm_Vertical | ~
 | Pacman | J9 | JST PH | Connector_JST:JST_PH_B4B-PH-K_1x04_P2.00mm_Vertical | ~
 | Pacman | J9 | JST PH | Connector_JST:JST_PH_B4B-PH-K_1x04_P2.00mm_Vertical | ~
 | DEMO | JP1 | SolderJumper_2_Bridged | Jumper:SolderJumper-2_P1.3mm_Bridged_RoundedPad1.0x1.5mm | ~
 | DCB | JP1 | SolderJumper_2_Bridged | Jumper:SolderJumper-2_P1.3mm_Bridged_Pad1.0x1.5mm | ~
 | HVB | JP1 | SolderJumper_2_Bridged | Jumper:SolderJumper-2_P1.3mm_Bridged_RoundedPad1.0x1.5mm | ~
 | RCB | JP1 | SolderJumper_2_Bridged | Jumper:SolderJumper-2_P1.3mm_Bridged_Pad1.0x1.5mm | ~
Order | Pacman | K1 | G2RL | AERO_Footprints:G2RL | http://omronfs.omron.com/en_US/ecb/products/pdf/en-g5v_1.pdf
Order | Pacman | K1 | G2RL | AERO_Footprints:G2RL | http://omronfs.omron.com/en_US/ecb/products/pdf/en-g5v_1.pdf
Order | RCB | K1 | T9VV1K15-12S | AERO-footprints:RELAY_T9VV1K15-12S | https://www.te.com/commerce/DocumentDelivery/DDEController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
In Stock | Pacman | K2 | G5V-1 | Relay_THT:Relay_SPDT_Omron_G5V-1 | http://omronfs.omron.com/en_US/ecb/products/pdf/en-g5v_1.pdf
In Stock | Pacman | K2 | G5V-1 | Relay_THT:Relay_SPDT_Omron_G5V-1 | http://omronfs.omron.com/en_US/ecb/products/pdf/en-g5v_1.pdf
In Stock | RCB | K2 | G5V-2 | Relay_THT:Relay_DPDT_Omron_G5V-2 | http://omronfs.omron.com/en_US/ecb/products/pdf/en-g5v_2.pdf
In Stock | Pacman | K3 | G5V-1 | Relay_THT:Relay_SPDT_Omron_G5V-1 | http://omronfs.omron.com/en_US/ecb/products/pdf/en-g5v_1.pdf
In Stock | Pacman | K3 | G5V-1 | Relay_THT:Relay_SPDT_Omron_G5V-1 | http://omronfs.omron.com/en_US/ecb/products/pdf/en-g5v_1.pdf
In Stock | RCB | K3 | G5V-2 | Relay_THT:Relay_DPDT_Omron_G5V-2 | http://omronfs.omron.com/en_US/ecb/products/pdf/en-g5v_2.pdf
 | HVB | L1 | 1uH | Inductor_SMD:L_1008_2520Metric_Pad1.43x2.20mm_HandSolder | ~
 | HVB | L2 | 0.15uH | Inductor_SMD:L_0805_2012Metric_Pad1.15x1.40mm_HandSolder | ~
In Stock | DCB | Q1 | 2N7002 | Package_TO_SOT_SMD:SOT-23 | https://www.onsemi.com/pub/Collateral/NDS7002A-D.PDF
In Stock | HVB | Q1 | PSMN5R2-60YL | Package_TO_SOT_SMD:LFPAK56 | https://assets.nexperia.com/documents/data-sheet/PSMN5R2-60YL.pdf
In Stock | HVB | Q2 | PSMN5R2-60YL | Package_TO_SOT_SMD:LFPAK56 | https://assets.nexperia.com/documents/data-sheet/PSMN5R2-60YL.pdf
In Stock | Pacman | Q2 | MMBT2222A | Package_TO_SOT_SMD:SOT-23 | ~
In Stock | Pacman | Q2 | MMBT2222A | Package_TO_SOT_SMD:SOT-23 | ~
In Stock | HVB | Q3 | DMN3404L | Package_TO_SOT_SMD:SOT-23_Handsoldering | ~
In Stock | DEMO | R1 | 330 | Resistor_SMD:R_0603_1608Metric_Pad0.98x0.95mm_HandSolder | ~
In Stock | DCB | R1 | 10k | Resistor_SMD:R_0603_1608Metric_Pad0.98x0.95mm_HandSolder | ~
In Stock | EMRAX | R1 | 10k | Resistor_SMD:R_0603_1608Metric_Pad0.98x0.95mm_HandSolder | ~
Order | HVB | R1 | 39k | Resistor_THT:R_Axial_DIN0411_L9.9mm_D3.6mm_P25.40mm_Horizontal | ~
Order | Pacman | R1 | 39k | Resistor_THT:R_Axial_DIN0414_L11.9mm_D4.5mm_P25.40mm_Horizontal | ~
Order | Pacman | R1 | 39k | Resistor_THT:R_Axial_DIN0414_L11.9mm_D4.5mm_P25.40mm_Horizontal | ~
In Stock | RCB | R1 | 20k | Resistor_SMD:R_0603_1608Metric_Pad0.98x0.95mm_HandSolder | ~
In Stock | DEMO | R10 | 100 | Resistor_SMD:R_0603_1608Metric_Pad0.98x0.95mm_HandSolder | ~
In Stock | DCB | R10 | 100 | Resistor_SMD:R_0603_1608Metric_Pad0.98x0.95mm_HandSolder | ~
In Stock | HVB | R10 | 10k | Resistor_THT:R_Axial_Power_L50.0mm_W9.0mm_P60.96mm | ~
In Stock | RCB | R10 | 100 | Resistor_SMD:R_0603_1608Metric_Pad0.98x0.95mm_HandSolder | ~
In Stock | HVB | R11 | 100 | Resistor_SMD:R_0603_1608Metric_Pad0.98x0.95mm_HandSolder | ~
Order | RCB | R11 | 1.5K | Resistor_SMD:R_0603_1608Metric_Pad0.98x0.95mm_HandSolder | ~
In Stock | HVB | R12 | 10k | Resistor_SMD:R_0603_1608Metric_Pad0.98x0.95mm_HandSolder | ~
Order | RCB | R12 | 1.5K | Resistor_SMD:R_0603_1608Metric_Pad0.98x0.95mm_HandSolder | ~
In Stock | HVB | R13 | 120 | Resistor_SMD:R_0603_1608Metric_Pad0.98x0.95mm_HandSolder | ~
Order | RCB | R13 | 1.5K | Resistor_SMD:R_0603_1608Metric_Pad0.98x0.95mm_HandSolder | ~
In Stock | RCB | R14 | 20k | Resistor_SMD:R_0603_1608Metric_Pad0.98x0.95mm_HandSolder | ~
In Stock | HVB | R15 | 1 | Resistor_SMD:R_2512_6332Metric_Pad1.40x3.35mm_HandSolder | ~
Order | RCB | R15 | 50k | Resistor_SMD:R_0603_1608Metric_Pad0.98x0.95mm_HandSolder | ~
In Stock | RCB | R16 | 20k | Resistor_SMD:R_0603_1608Metric_Pad0.98x0.95mm_HandSolder | ~
In Stock | HVB | R17 | 1k | Resistor_SMD:R_0603_1608Metric_Pad0.98x0.95mm_HandSolder | ~
In Stock | RCB | R17 | 200k | Resistor_SMD:R_0603_1608Metric_Pad0.98x0.95mm_HandSolder | ~
In Stock | HVB | R18 | 1k | Resistor_SMD:R_0603_1608Metric_Pad0.98x0.95mm_HandSolder | ~
In Stock | HVB | R19 | 10k | Resistor_SMD:R_0603_1608Metric_Pad0.98x0.95mm_HandSolder | ~
In Stock | DEMO | R2 | 330 | Resistor_SMD:R_0603_1608Metric_Pad0.98x0.95mm_HandSolder | ~
In Stock | DCB | R2 | 330 | Resistor_SMD:R_0603_1608Metric_Pad0.98x0.95mm_HandSolder | ~
In Stock | HVB | R2 | 10k | Resistor_SMD:R_0603_1608Metric_Pad0.98x0.95mm_HandSolder | ~
In Stock | Pacman | R2 | 120 | Resistor_SMD:R_0603_1608Metric_Pad0.98x0.95mm_HandSolder | ~
In Stock | Pacman | R2 | 120 | Resistor_SMD:R_0603_1608Metric_Pad0.98x0.95mm_HandSolder | ~
In Stock | RCB | R2 | 330 | Resistor_SMD:R_0603_1608Metric_Pad0.98x0.95mm_HandSolder | ~
In Stock | HVB | R20 | 1 | Resistor_SMD:R_2512_6332Metric_Pad1.40x3.35mm_HandSolder | ~
In Stock | HVB | R3 | 100k | Resistor_SMD:R_0603_1608Metric_Pad0.98x0.95mm_HandSolder | ~
Order | Pacman | R3 | 500 | Package_TO_SOT_THT:TO-220-2_Horizontal_TabDown | ~
Order | Pacman | R3 | 500 | Package_TO_SOT_THT:TO-220-2_Horizontal_TabDown | ~
In Stock | RCB | R3 | 10k | Resistor_SMD:R_0603_1608Metric_Pad0.98x0.95mm_HandSolder | ~
Order | HVB | R4 | 235k | Resistor_SMD:R_0603_1608Metric_Pad0.98x0.95mm_HandSolder | ~
In Stock | RCB | R4 | 1k | Resistor_SMD:R_0603_1608Metric_Pad0.98x0.95mm_HandSolder | ~
In Stock | HVB | R5 | 10k | Resistor_SMD:R_0603_1608Metric_Pad0.98x0.95mm_HandSolder | ~
In Stock | Pacman | R5 | 10k | Resistor_SMD:R_0603_1608Metric | ~
In Stock | Pacman | R5 | 10k | Resistor_SMD:R_0603_1608Metric | ~
In Stock | RCB | R5 | 10K | Resistor_SMD:R_0603_1608Metric_Pad0.98x0.95mm_HandSolder | ~
In Stock | DEMO | R6 | 120 | Resistor_SMD:R_0603_1608Metric_Pad0.98x0.95mm_HandSolder | ~
In Stock | DCB | R6 | 120 | Resistor_SMD:R_0603_1608Metric_Pad0.98x0.95mm_HandSolder | ~
Order | HVB | R6 | 0.75 | Resistor_SMD:R_2512_6332Metric_Pad1.40x3.35mm_HandSolder | ~
In Stock | Pacman | R6 | 2k | Resistor_SMD:R_0603_1608Metric | ~
In Stock | Pacman | R6 | 2k | Resistor_SMD:R_0603_1608Metric | ~
In Stock | RCB | R6 | 120 | Resistor_SMD:R_0603_1608Metric_Pad0.98x0.95mm_HandSolder | ~
In Stock | HVB | R7 | 330 | Resistor_SMD:R_0603_1608Metric_Pad0.98x0.95mm_HandSolder | ~
In Stock | RCB | R7 | 1k | Resistor_SMD:R_0603_1608Metric_Pad0.98x0.95mm_HandSolder | ~
In Stock | HVB | R8 | 300 | Resistor_SMD:R_0603_1608Metric_Pad0.98x0.95mm_HandSolder | ~
In Stock | RCB | R8 | 2.2K | Resistor_SMD:R_0603_1608Metric_Pad0.98x0.95mm_HandSolder | ~
In Stock | HVB | R9 | 10k | Resistor_THT:R_Axial_Power_L50.0mm_W9.0mm_P60.96mm | ~
Order | RCB | R9 | 50k | Resistor_SMD:R_0603_1608Metric_Pad0.98x0.95mm_HandSolder | ~
In Stock | DCB | RN1 | R_Pack04 | Resistor_SMD:R_Array_Convex_4x1206 | ~
In Stock | HVB | RV1 | 50k TC33x-2-503E | Potentiometer_SMD:Potentiometer_Bourns_TC33X_Vertical
Order | DEMO | U1 | STM32F413CGUx | Package_DFN_QFN:QFN-48-1EP_7x7mm_P0.5mm_EP5.6x5.6mm | http://www.st.com/st-web-ui/static/active/en/resource/technical/document/datasheet/DM00282249.pdf
Order | DCB | U1 | STM32F413CGUx | Package_DFN_QFN:QFN-48-1EP_7x7mm_P0.5mm_EP5.6x5.6mm | http://www.st.com/st-web-ui/static/active/en/resource/technical/document/datasheet/DM00282249.pdf
Order | HVB | U1 | MAX33054EASA+T | AERO_Footprints:SOIC127P600X175-8N
Order | RCB | U1 | STM32F413CGUx | Package_DFN_QFN:QFN-48-1EP_7x7mm_P0.5mm_EP5.6x5.6mm | http://www.st.com/st-web-ui/static/active/en/resource/technical/document/datasheet/DM00282249.pdf
Order | DEMO | U2 | LD1117S33TR_SOT223 | Package_TO_SOT_SMD:SOT-223-3_TabPin2 | http://www.st.com/st-web-ui/static/active/en/resource/technical/document/datasheet/CD00000544.pdf
In Stock | HVB | U2 | LTV-817S | Package_DIP:SMDIP-4_W9.53mm_Clearance8mm | http://www.us.liteon.com/downloads/LTV-817-827-847.PDF
Order | DCB | U3 | LDL1117S33R | Package_TO_SOT_SMD:SOT-223-3_TabPin2 | http://www.st.com/st-web-ui/static/active/en/resource/technical/document/datasheet/CD00000544.pdf
Order | HVB | U3 | LM555xM | Package_SO:SOIC-8_3.9x4.9mm_P1.27mm | http://www.ti.com/lit/ds/symlink/lm555.pdf
Order | RCB | U3 | LDL1117S33R | Package_TO_SOT_SMD:SOT-223-3_TabPin2 | http://www.st.com/st-web-ui/static/active/en/resource/technical/document/datasheet/CD00000544.pdf
Order | DEMO | U4 | MAX33054EASA+T | AERO_Footprints:SOIC127P600X175-8N
Order | DCB | U4 | MAX33054EASA+T | AERO_Footprints:SOIC127P600X175-8N
Order | HVB | U4 | LD1117S33TR_SOT223 | Package_TO_SOT_SMD:SOT-223-3_TabPin2 | http://www.st.com/st-web-ui/static/active/en/resource/technical/document/datasheet/CD00000544.pdf
Order | RCB | U4 | MAX33054EASA+T | AERO_Footprints:SOIC127P600X175-8N
Order | HVB | U5 | STM32F413CGUx | Package_DFN_QFN:QFN-48-1EP_7x7mm_P0.5mm_EP5.3x5.3mm | http://www.st.com/st-web-ui/static/active/en/resource/technical/document/datasheet/DM00282249.pdf
 | RCB | U5 | BV1HAL45EFJ | Package_SO:HTSOP-8-1EP_3.9x4.9mm_P1.27mm_EP2.4x3.2mm_ThermalVias | https://fscdn.rohm.com/en/products/databook/datasheet/ic/power/power_switch/bv1hal45efj-e.pdf
 | RCB | U6 | BV1HAL45EFJ | Package_SO:HTSOP-8-1EP_3.9x4.9mm_P1.27mm_EP2.4x3.2mm_ThermalVias | https://fscdn.rohm.com/en/products/databook/datasheet/ic/power/power_switch/bv1hal45efj-e.pdf
Custom | HVB | U7 | Vicor_AERO | AERO_Footprints:vicor-socket-no-cutouts
 | RCB | U7 | BV1HAL45EFJ | Package_SO:HTSOP-8-1EP_3.9x4.9mm_P1.27mm_EP2.4x3.2mm_ThermalVias | https://fscdn.rohm.com/en/products/databook/datasheet/ic/power/power_switch/bv1hal45efj-e.pdf
In Stock | HVB | U8 | LTV-817S | Package_DIP:SMDIP-4_W9.53mm_Clearance8mm | http://www.us.liteon.com/downloads/LTV-817-827-847.PDF
 | HVB | U9 | TLP184 | Package_SO:MFSOP6-4_4.4x3.6mm_P1.27mm | https://toshiba.semicon-storage.com/info/docget.jsp?did=11793&prodName=TLP184
 | DEMO | Y1 | CSTNE8M00 | AERO_Footprints:Resonator_SMD_muRata_CSTxExxV-3Pin_3.0x1.1mm_HandSoldering | ~
 | DCB | Y1 | CSTNE8M00 | AERO_Footprints:Resonator_SMD_muRata_CSTxExxV-3Pin_3.0x1.1mm_HandSoldering | ~
 | HVB | Y1 | CSTME8M00 | AERO_Footprints:Resonator_SMD_muRata_CSTxExxV-3Pin_3.0x1.1mm_HandSoldering | ~
 | RCB | Y1 | CSTNE8M00 | AERO_Footprints:Resonator_SMD_muRata_CSTxExxV-3Pin_3.0x1.1mm_HandSoldering | ~

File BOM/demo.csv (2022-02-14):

Source: | C:\Users\aero\Documents\GitHub\AERO_2021-2022\demo\board\demo\demo.kicad_sch
Date: | 2/14/2022 9:48:41 AM
Tool: | Eeschema (6.0.1)
Component Count: | 25
Ref | Value | Footprint | Datasheet | Manufacturer | Vendor
C2 | .1u | Capacitor_SMD:C_0603_1608Metric_Pad1.08x0.95mm_HandSolder | ~
C3 | 10u | Capacitor_SMD:C_0603_1608Metric_Pad1.08x0.95mm_HandSolder | ~
C4 | 4.7u | Capacitor_SMD:C_0603_1608Metric_Pad1.08x0.95mm_HandSolder | ~
C5 | 0.1u | Capacitor_SMD:C_0603_1608Metric_Pad1.08x0.95mm_HandSolder | ~
C7 | 0.1u | Capacitor_SMD:C_0603_1608Metric_Pad1.08x0.95mm_HandSolder | ~
C8 | 0.1u | Capacitor_SMD:C_0603_1608Metric_Pad1.08x0.95mm_HandSolder | ~
C9 | 0.1u | Capacitor_SMD:C_0603_1608Metric_Pad1.08x0.95mm_HandSolder | ~
C10 | 0.1u | Capacitor_SMD:C_0603_1608Metric_Pad1.08x0.95mm_HandSolder | ~
C11 | 0.1u | Capacitor_SMD:C_0603_1608Metric_Pad1.08x0.95mm_HandSolder | ~
C12 | 0.1u | Capacitor_SMD:C_0603_1608Metric_Pad1.08x0.95mm_HandSolder | ~
D1 | LED | LED_SMD:LED_0603_1608Metric_Pad1.05x0.95mm_HandSolder | ~
D2 | LED | LED_SMD:LED_0603_1608Metric_Pad1.05x0.95mm_HandSolder | ~
D9 | DESD2CAN2SOQ-7 | Package_TO_SOT_SMD:SOT-23 | http://www.onsemi.com/pub_link/Collateral/NUP2105L-D.PDF
J2 | Conn_01x20 | Connector_PinHeader_2.54mm:PinHeader_1x20_P2.54mm_Vertical | ~
J3 | Conn_01x20 | Connector_PinHeader_2.54mm:PinHeader_1x20_P2.54mm_Vertical | ~
J6 | FTSH-107-01-F-DV-K | Connector_PinHeader_1.27mm:PinHeader_2x07_P1.27mm_Vertical_SMD | ~
JP1 | SolderJumper_2_Bridged | Jumper:SolderJumper-2_P1.3mm_Bridged_RoundedPad1.0x1.5mm | ~
R1 | 330 | Resistor_SMD:R_0603_1608Metric_Pad0.98x0.95mm_HandSolder | ~
R2 | 330 | Resistor_SMD:R_0603_1608Metric_Pad0.98x0.95mm_HandSolder | ~
R6 | 120 | Resistor_SMD:R_0603_1608Metric_Pad0.98x0.95mm_HandSolder | ~
R10 | 100 | Resistor_SMD:R_0603_1608Metric_Pad0.98x0.95mm_HandSolder | ~
U1 | STM32F413CGUx | Package_DFN_QFN:QFN-48-1EP_7x7mm_P0.5mm_EP5.6x5.6mm | http://www.st.com/st-web-ui/static/active/en/resource/technical/document/datasheet/DM00282249.pdf
U2 | LD1117S33TR_SOT223 | Package_TO_SOT_SMD:SOT-223-3_TabPin2 | http://www.st.com/st-web-ui/static/active/en/resource/technical/document/datasheet/CD00000544.pdf
U4 | MAX33054EASA+T | AERO_Footprints:SOIC127P600X175-8N
Y1 | CSTNE8M00 | AERO_Footprints:Resonator_SMD_muRata_CSTxExxV-3Pin_3.0x1.1mm_HandSoldering | ~

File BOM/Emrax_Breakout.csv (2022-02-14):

Source: | C:\Users\aero\Documents\GitHub\AERO_2021-2022\emrax_board\Emrax_Breakout.kicad_sch
Date: | 2/14/2022 9:55:46 AM
Tool: | Eeschema (6.0.1)
Component Count: | 4
Ref | Value | Footprint | Datasheet | Manufacturer | Vendor
J1 | Conn_01x08 | AERO_Footprints:TE_1-776280-1_8pin_Horizontal | ~
J2 | Conn_01x06 | Connector_JST:JST_XH_S6B-XH-A-1_1x06_P2.50mm_Horizontal | ~
J3 | Conn_01x02 | Connector_JST:JST_XH_S2B-XH-A-1_1x02_P2.50mm_Horizontal | ~
R1 | R | Resistor_SMD:R_0603_1608Metric_Pad0.98x0.95mm_HandSolder | ~

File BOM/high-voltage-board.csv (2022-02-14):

Source: | C:\Users\aero\Documents\GitHub\AERO_2021-2022\HVB\high-voltage-board\high-voltage-board.kicad_sch
Date: | 2/14/2022 9:57:00 AM
Tool: | Eeschema (6.0.1)
Component Count: | 72
Ref | Value | Footprint | Datasheet | Manufacturer | Vendor
C1 | 4.7u | Capacitor_SMD:C_0603_1608Metric_Pad1.08x0.95mm_HandSolder | ~
C2 | 0.68uF | Capacitor_THT:C_Rect_L18.0mm_W8.0mm_P15.00mm_FKS3_FKP3 | ~
C3 | 0.1u | Capacitor_SMD:C_0603_1608Metric_Pad1.08x0.95mm_HandSolder | ~
C4 | 0.1u | Capacitor_SMD:C_0603_1608Metric_Pad1.08x0.95mm_HandSolder | ~
C5 | 0.1u | Capacitor_SMD:C_0603_1608Metric_Pad1.08x0.95mm_HandSolder | ~
C6 | 1u | Capacitor_SMD:C_0603_1608Metric_Pad1.08x0.95mm_HandSolder | ~
C7 | 0.1u | Capacitor_SMD:C_0603_1608Metric_Pad1.08x0.95mm_HandSolder | ~
C9 | .1u | Capacitor_SMD:C_0603_1608Metric_Pad1.08x0.95mm_HandSolder | ~
C10 | 0.1u | Capacitor_SMD:C_0603_1608Metric_Pad1.08x0.95mm_HandSolder | ~
C12 | 10u | Capacitor_SMD:C_0603_1608Metric_Pad1.08x0.95mm_HandSolder | ~
C13 | 0.1u | Capacitor_SMD:C_0603_1608Metric_Pad1.08x0.95mm_HandSolder | ~
C15 | 0.1u | Capacitor_SMD:C_0603_1608Metric_Pad1.08x0.95mm_HandSolder | ~
C16 | 0.1u | Capacitor_SMD:C_0603_1608Metric_Pad1.08x0.95mm_HandSolder | ~
C17 | 0.1u | Capacitor_SMD:C_0603_1608Metric_Pad1.08x0.95mm_HandSolder | ~
C19 | 0.68uF | Capacitor_THT:C_Rect_L18.0mm_W8.0mm_P15.00mm_FKS3_FKP3 | ~
C22 | 4700uF | Capacitor_THT:C_Radial_D18.0mm_H35.5mm_P7.50mm | ~
C23 | 4700uF | Capacitor_THT:C_Radial_D18.0mm_H35.5mm_P7.50mm | ~
D1 | BAT54GW | Diode_SMD:D_SOD-123 | ~
D2 | LED | LED_SMD:LED_0603_1608Metric_Pad1.05x0.95mm_HandSolder | ~
D3 | SP0502BAHT | Package_TO_SOT_SMD:SOT-23 | http://www.littelfuse.com/~/media/files/littelfuse/technical%20resources/documents/data%20sheets/sp05xxba.pdf
F1 | 2A | Fuse:Fuseholder_Cylinder-5x20mm_Schurter_0031_8201_Horizontal_Open | ~
F2 | 35A | Fuse:Fuseholder_Cylinder-5x20mm_Schurter_0031_8201_Horizontal_Open | ~
H1 | MountingHole | MountingHole:MountingHole_3.2mm_M3 | ~
H2 | MountingHole | MountingHole:MountingHole_3.2mm_M3 | ~
H3 | MountingHole | MountingHole:MountingHole_3.2mm_M3 | ~
H4 | MountingHole | MountingHole:MountingHole_3.2mm_M3 | ~
J1 | Conn_01x23 | AERO_Footprints:TE_1-770669-1_23pin_Horizontal | ~
J2 | HECS | Connector_JST:JST_XH_B5B-XH-A_1x05_P2.50mm_Vertical | ~
J3 | HV+ | Connector_Hirose:Hirose_DF63M-1P-3.96DSA_1x01_P3.96mm_Vertical | ~
J4 | HV- | Connector_Hirose:Hirose_DF63M-1P-3.96DSA_1x01_P3.96mm_Vertical | ~
J5 | HV+ | AERO_Footprints:TE_MATE-N-LOK_1-770870-x_1x03_P4.14mm_Vertical | ~
J6 | HV- | AERO_Footprints:TE_MATE-N-LOK_1-770870-x_1x03_P4.14mm_Vertical | ~
J7 | Conn_01x02 | Connector_JST:JST_XH_B2B-XH-A_1x02_P2.50mm_Vertical | ~
J8 | HV+ | Connector_Hirose:Hirose_DF63M-1P-3.96DSA_1x01_P3.96mm_Vertical | ~
J9 | Bender-LV | Connector_JST:JST_XH_B5B-XH-A_1x05_P2.50mm_Vertical | ~
J10 | FTSH-107-01-F-DV-k | Connector_PinHeader_1.27mm:PinHeader_2x07_P1.27mm_Vertical_SMD | ~
J11 | HV- | Connector_Hirose:Hirose_DF63M-1P-3.96DSA_1x01_P3.96mm_Vertical | ~
J12 | Conn_01x02 | Connector_JST:JST_XH_B2B-XH-A_1x02_P2.50mm_Vertical | ~
JP1 | SolderJumper_2_Bridged | Jumper:SolderJumper-2_P1.3mm_Bridged_RoundedPad1.0x1.5mm | ~
L1 | 1uH | Inductor_SMD:L_1008_2520Metric_Pad1.43x2.20mm_HandSolder | ~
L2 | 0.15uH | Inductor_SMD:L_0805_2012Metric_Pad1.15x1.40mm_HandSolder | ~
Q1 | PSMN5R2-60YL | Package_TO_SOT_SMD:LFPAK56 | https://assets.nexperia.com/documents/data-sheet/PSMN5R2-60YL.pdf
Q2 | PSMN5R2-60YL | Package_TO_SOT_SMD:LFPAK56 | https://assets.nexperia.com/documents/data-sheet/PSMN5R2-60YL.pdf
Q3 | DMN3404L | Package_TO_SOT_SMD:SOT-23_Handsoldering | ~
R1 | 39k | Resistor_THT:R_Axial_DIN0411_L9.9mm_D3.6mm_P25.40mm_Horizontal | ~
R2 | 10k | Resistor_SMD:R_0603_1608Metric_Pad0.98x0.95mm_HandSolder | ~
R3 | 100k | Resistor_SMD:R_0603_1608Metric_Pad0.98x0.95mm_HandSolder | ~
R4 | 235k | Resistor_SMD:R_0603_1608Metric_Pad0.98x0.95mm_HandSolder | ~
R5 | 10k | Resistor_SMD:R_0603_1608Metric_Pad0.98x0.95mm_HandSolder | ~
R6 | 0.75 | Resistor_SMD:R_2512_6332Metric_Pad1.40x3.35mm_HandSolder | ~
R7 | 330 | Resistor_SMD:R_0603_1608Metric_Pad0.98x0.95mm_HandSolder | ~
R8 | 300 | Resistor_SMD:R_0603_1608Metric_Pad0.98x0.95mm_HandSolder | ~
R9 | 10k | Resistor_THT:R_Axial_Power_L50.0mm_W9.0mm_P60.96mm | ~
R10 | 10k | Resistor_THT:R_Axial_Power_L50.0mm_W9.0mm_P60.96mm | ~
R11 | 100 | Resistor_SMD:R_0603_1608Metric_Pad0.98x0.95mm_HandSolder | ~
R12 | 10k | Resistor_SMD:R_0603_1608Metric_Pad0.98x0.95mm_HandSolder | ~
R13 | 120 | Resistor_SMD:R_0603_1608Metric_Pad0.98x0.95mm_HandSolder | ~
R15 | 1 | Resistor_SMD:R_2512_6332Metric_Pad1.40x3.35mm_HandSolder | ~
R17 | 1k | Resistor_SMD:R_0603_1608Metric_Pad0.98x0.95mm_HandSolder | ~
R18 | 1k | Resistor_SMD:R_0603_1608Metric_Pad0.98x0.95mm_HandSolder | ~
R19 | 10k | Resistor_SMD:R_0603_1608Metric_Pad0.98x0.95mm_HandSolder | ~
R20 | 1 | Resistor_SMD:R_2512_6332Metric_Pad1.40x3.35mm_HandSolder | ~
RV1 | 50k TC33x-2-503E | Potentiometer_SMD:Potentiometer_Bourns_TC33X_Vertical
U1 | MAX33054EASA+T | AERO_Footprints:SOIC127P600X175-8N
U2 | LTV-817S | Package_DIP:SMDIP-4_W9.53mm_Clearance8mm | http://www.us.liteon.com/downloads/LTV-817-827-847.PDF
U3 | LM555xM | Package_SO:SOIC-8_3.9x4.9mm_P1.27mm | http://www.ti.com/lit/ds/symlink/lm555.pdf
U4 | LD1117S33TR_SOT223 | Package_TO_SOT_SMD:SOT-223-3_TabPin2 | http://www.st.com/st-web-ui/static/active/en/resource/technical/document/datasheet/CD00000544.pdf
U5 | STM32F413CGUx | Package_DFN_QFN:QFN-48-1EP_7x7mm_P0.5mm_EP5.3x5.3mm | http://www.st.com/st-web-ui/static/active/en/resource/technical/document/datasheet/DM00282249.pdf
U7 | Vicor_AERO | AERO_Footprints:vicor-socket-no-cutouts
U8 | LTV-817S | Package_DIP:SMDIP-4_W9.53mm_Clearance8mm | http://www.us.liteon.com/downloads/LTV-817-827-847.PDF
U9 | TLP184 | Package_SO:MFSOP6-4_4.4x3.6mm_P1.27mm | https://toshiba.semicon-storage.com/info/docget.jsp?did=11793&prodName=TLP184
Y1 | CSTME8M00 | AERO_Footprints:Resonator_SMD_muRata_CSTxExxV-3Pin_3.0x1.1mm_HandSoldering | ~

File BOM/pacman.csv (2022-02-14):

Source: | C:\Users\aero\Documents\GitHub\AERO_2021-2022\PAM\pacman\pacman.kicad_sch
Date: | 2/14/2022 9:58:17 AM
Tool: | Eeschema (6.0.1)
Component Count: | 23
Ref | Value | Footprint | Datasheet | Manufacturer | Vendor
D1 | LED | AERO_Footprints:LPA-C011301S-x LED 0805 LIGHT PIPE SINGLE VERT SMD | ~
D3 | 1N4148 | Diode_SMD:D_MiniMELF | http://www.nxp.com/documents/data_sheet/1N4148_1N4448.pdf
D4 | 1N4148 | Diode_SMD:D_MiniMELF | http://www.nxp.com/documents/data_sheet/1N4148_1N4448.pdf
D5 | MMBZxx | Package_TO_SOT_SMD:SOT-23 | http://www.onsemi.com/pub/Collateral/MMBZ5V6ALT1-D.PDF
F1 | 1A 300VDC | AERO_Footprints:Fuseholder_Cylinder-5x20mm_Schurter_0031_8201_Horizontal_Open_3d | ~
F2 | 1A 300VDC | AERO_Footprints:Fuseholder_Cylinder-5x20mm_Schurter_0031_8201_Horizontal_Open_3d | ~
F3 | Fuse | AERO_Footprints:Fuseholder_Blade_Mini_Keystone_3568 | ~
J1 | Conn_01x08 | AERO_Footprints:TE_1-776276-1_8pin_Vertical | ~
J2 | Conn_01x04 | Connector_JST:JST_XH_B4B-XH-A_1x04_P2.50mm_Vertical | ~
J3 | Conn_01x01 | Connector_Hirose:Hirose_DF63M-1P-3.96DSA_1x01_P3.96mm_Vertical | ~
J4 | Conn_01x01 | Connector_Hirose:Hirose_DF63M-1P-3.96DSA_1x01_P3.96mm_Vertical | ~
J5 | Conn_01x01 | Connector_Hirose:Hirose_DF63M-1P-3.96DSA_1x01_P3.96mm_Vertical | ~
J6 | Conn_01x02 | Connector_JST:JST_XH_B2B-XH-A_1x02_P2.50mm_Vertical | ~
J9 | JST PH | Connector_JST:JST_PH_B4B-PH-K_1x04_P2.00mm_Vertical | ~
K1 | G2RL | AERO_Footprints:G2RL | http://omronfs.omron.com/en_US/ecb/products/pdf/en-g5v_1.pdf
K2 | G5V-1 | Relay_THT:Relay_SPDT_Omron_G5V-1 | http://omronfs.omron.com/en_US/ecb/products/pdf/en-g5v_1.pdf
K3 | G5V-1 | Relay_THT:Relay_SPDT_Omron_G5V-1 | http://omronfs.omron.com/en_US/ecb/products/pdf/en-g5v_1.pdf
Q2 | MMBT2222A | Package_TO_SOT_SMD:SOT-23 | ~
R1 | 39k | Resistor_THT:R_Axial_DIN0414_L11.9mm_D4.5mm_P25.40mm_Horizontal | ~
R2 | 120 | Resistor_SMD:R_0603_1608Metric_Pad0.98x0.95mm_HandSolder | ~
R3 | 500 | Package_TO_SOT_THT:TO-220-2_Horizontal_TabDown | ~
R5 | 10k | Resistor_SMD:R_0603_1608Metric | ~
R6 | 2k | Resistor_SMD:R_0603_1608Metric | ~

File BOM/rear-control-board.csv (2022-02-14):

Source: | C:\Users\aero\Documents\GitHub\AERO_2021-2022\RCB\rear-control-board\rear-control-board.kicad_sch
Date: | 2/14/2022 9:59:48 AM
Tool: | Eeschema (6.0.1)
Component Count: | 68
Ref | Value | Footprint | Datasheet | Manufacturer | Vendor
C1 | .1u | Capacitor_SMD:C_0603_1608Metric_Pad1.08x0.95mm_HandSolder | ~
C2 | 1u | Capacitor_SMD:C_0603_1608Metric_Pad1.08x0.95mm_HandSolder | ~
C3 | 1u | Capacitor_SMD:C_0603_1608Metric_Pad1.08x0.95mm_HandSolder | ~
C4 | 4.7u | Capacitor_SMD:C_0603_1608Metric_Pad1.08x0.95mm_HandSolder | ~
C5 | 0.1u | Capacitor_SMD:C_0603_1608Metric_Pad1.08x0.95mm_HandSolder | ~
C6 | 10u | Capacitor_SMD:C_0603_1608Metric_Pad1.08x0.95mm_HandSolder | ~
C7 | 0.1u | Capacitor_SMD:C_0603_1608Metric_Pad1.08x0.95mm_HandSolder | ~
C8 | 0.1u | Capacitor_SMD:C_0603_1608Metric_Pad1.08x0.95mm_HandSolder | ~
C9 | 0.1u | Capacitor_SMD:C_0603_1608Metric_Pad1.08x0.95mm_HandSolder | ~
C10 | 0.1u | Capacitor_SMD:C_0603_1608Metric_Pad1.08x0.95mm_HandSolder | ~
C11 | 0.1u | Capacitor_SMD:C_0603_1608Metric_Pad1.08x0.95mm_HandSolder | ~
C12 | 0.1u | Capacitor_SMD:C_0603_1608Metric_Pad1.08x0.95mm_HandSolder | ~
C13 | 1u | Capacitor_SMD:C_0603_1608Metric_Pad1.08x0.95mm_HandSolder | ~
D1 | LED | LED_SMD:LED_0603_1608Metric_Pad1.05x0.95mm_HandSolder | ~
D3 | D_KAK | Package_TO_SOT_SMD:TO-252-2 | ~
D4 | 1N4148 | Diode_SMD:D_SOD-123 | https://assets.nexperia.com/documents/data-sheet/1N4148_1N4448.pdf
D5 | 1N4148 | Diode_SMD:D_SOD-123 | https://assets.nexperia.com/documents/data-sheet/1N4148_1N4448.pdf
D6 | SP0502BAHT | Package_TO_SOT_SMD:SOT-23 | http://www.littelfuse.com/~/media/files/littelfuse/technical%20resources/documents/data%20sheets/sp05xxba.pdf
D7 | SP0502BAHT | Package_TO_SOT_SMD:SOT-23 | http://www.littelfuse.com/~/media/files/littelfuse/technical%20resources/documents/data%20sheets/sp05xxba.pdf
D8 | SP0502BAHT | Package_TO_SOT_SMD:SOT-23 | http://www.littelfuse.com/~/media/files/littelfuse/technical%20resources/documents/data%20sheets/sp05xxba.pdf
D9 | DESD2CAN2SOQ-7 | Package_TO_SOT_SMD:SOT-23 | http://www.onsemi.com/pub_link/Collateral/NUP2105L-D.PDF
F1 | 2A | AERO_Footprints:Fuseholder_Blade_Mini_Keystone_3568 | ~
F2 | 10A | AERO_Footprints:Fuseholder_Blade_Mini_Keystone_3568 | ~
F3 | 15A | AERO_Footprints:Fuseholder_Blade_Mini_Keystone_3568 | ~
F4 | 2A | AERO_Footprints:Fuseholder_Blade_Mini_Keystone_3568 | ~
F5 | 2A | AERO_Footprints:Fuseholder_Blade_Mini_Keystone_3568 | ~
F6 | 15A | AERO_Footprints:Fuseholder_Blade_Mini_Keystone_3568 | ~
F7 | 5A | AERO_Footprints:Fuseholder_Blade_Mini_Keystone_3568 | ~
F8 | 2A | AERO_Footprints:Fuseholder_Blade_Mini_Keystone_3568 | ~
F9 | 1A | AERO_Footprints:Fuseholder_Blade_Mini_Keystone_3568 | ~
F10 | 2A | AERO_Footprints:Fuseholder_Blade_Mini_Keystone_3568 | ~
F11 | 20A | AERO_Footprints:Fuseholder_Blade_Mini_Keystone_3568 | ~
H1 | MountingHole | MountingHole:MountingHole_3.2mm_M3 | ~
H2 | MountingHole | MountingHole:MountingHole_3.2mm_M3 | ~
J1 | Conn_01x23 | AERO_Footprints:TE_1-770669-1_23pin_Horizontal | ~
J2 | Conn_01x23 | AERO_Footprints:TE_1-770669-1_23pin_Horizontal | ~
J3 | Conn_01x08 | AERO_Footprints:TE_1-776280-1_8pin_Horizontal | ~
J4 | JST-B2B-VERT-2PIN | Connector_JST:JST_XH_B2B-XH-AM_1x02_P2.50mm_Vertical | ~
J5 | JST-B2B-VERT-2PIN | Connector_JST:JST_XH_B2B-XH-AM_1x02_P2.50mm_Vertical | ~
J6 | FTSH-107-01-F-DV-K | Connector_PinHeader_1.27mm:PinHeader_2x07_P1.27mm_Vertical_SMD | ~
JP1 | SolderJumper_2_Bridged | Jumper:SolderJumper-2_P1.3mm_Bridged_Pad1.0x1.5mm | ~
K1 | T9VV1K15-12S | AERO-footprints:RELAY_T9VV1K15-12S | https://www.te.com/commerce/DocumentDelivery/DDEController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
K2 | G5V-2 | Relay_THT:Relay_DPDT_Omron_G5V-2 | http://omronfs.omron.com/en_US/ecb/products/pdf/en-g5v_2.pdf
K3 | G5V-2 | Relay_THT:Relay_DPDT_Omron_G5V-2 | http://omronfs.omron.com/en_US/ecb/products/pdf/en-g5v_2.pdf
R1 | 20k | Resistor_SMD:R_0603_1608Metric_Pad0.98x0.95mm_HandSolder | ~
R2 | 330 | Resistor_SMD:R_0603_1608Metric_Pad0.98x0.95mm_HandSolder | ~
R3 | 10k | Resistor_SMD:R_0603_1608Metric_Pad0.98x0.95mm_HandSolder | ~
R4 | 1k | Resistor_SMD:R_0603_1608Metric_Pad0.98x0.95mm_HandSolder | ~
R5 | 10K | Resistor_SMD:R_0603_1608Metric_Pad0.98x0.95mm_HandSolder | ~
R6 | 120 | Resistor_SMD:R_0603_1608Metric_Pad0.98x0.95mm_HandSolder | ~
R7 | 1k | Resistor_SMD:R_0603_1608Metric_Pad0.98x0.95mm_HandSolder | ~
R8 | 2.2K | Resistor_SMD:R_0603_1608Metric_Pad0.98x0.95mm_HandSolder | ~
R9 | 50k | Resistor_SMD:R_0603_1608Metric_Pad0.98x0.95mm_HandSolder | ~
R10 | 100 | Resistor_SMD:R_0603_1608Metric_Pad0.98x0.95mm_HandSolder | ~
R11 | 1.5K | Resistor_SMD:R_0603_1608Metric_Pad0.98x0.95mm_HandSolder | ~
R12 | 1.5K | Resistor_SMD:R_0603_1608Metric_Pad0.98x0.95mm_HandSolder | ~
R13 | 1.5K | Resistor_SMD:R_0603_1608Metric_Pad0.98x0.95mm_HandSolder | ~
R14 | 20k | Resistor_SMD:R_0603_1608Metric_Pad0.98x0.95mm_HandSolder | ~
R15 | 50k | Resistor_SMD:R_0603_1608Metric_Pad0.98x0.95mm_HandSolder | ~
R16 | 20k | Resistor_SMD:R_0603_1608Metric_Pad0.98x0.95mm_HandSolder | ~
R17 | 200k | Resistor_SMD:R_0603_1608Metric_Pad0.98x0.95mm_HandSolder | ~
U1 | STM32F413CGUx | Package_DFN_QFN:QFN-48-1EP_7x7mm_P0.5mm_EP5.6x5.6mm | http://www.st.com/st-web-ui/static/active/en/resource/technical/document/datasheet/DM00282249.pdf
U3 | LDL1117S33R | Package_TO_SOT_SMD:SOT-223-3_TabPin2 | http://www.st.com/st-web-ui/static/active/en/resource/technical/document/datasheet/CD00000544.pdf
U4 | MAX33054EASA+T | AERO_Footprints:SOIC127P600X175-8N
U5 | BV1HAL45EFJ | Package_SO:HTSOP-8-1EP_3.9x4.9mm_P1.27mm_EP2.4x3.2mm_ThermalVias | https://fscdn.rohm.com/en/products/databook/datasheet/ic/power/power_switch/bv1hal45efj-e.pdf
U6 | BV1HAL45EFJ | Package_SO:HTSOP-8-1EP_3.9x4.9mm_P1.27mm_EP2.4x3.2mm_ThermalVias | https://fscdn.rohm.com/en/products/databook/datasheet/ic/power/power_switch/bv1hal45efj-e.pdf
U7 | BV1HAL45EFJ | Package_SO:HTSOP-8-1EP_3.9x4.9mm_P1.27mm_EP2.4x3.2mm_ThermalVias | https://fscdn.rohm.com/en/products/databook/datasheet/ic/power/power_switch/bv1hal45efj-e.pdf
Y1 | CSTNE8M00 | AERO_Footprints:Resonator_SMD_muRata_CSTxExxV-3Pin_3.0x1.1mm_HandSoldering | ~

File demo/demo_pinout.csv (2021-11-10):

Position | Name | Type | Signal | Label | AF0 | AF1 | AF2 | AF3 | AF4 | AF5 | AF6 | AF7 | AF8 | AF9 | AF10 | AF11 | AF12 | AF13 | AF14 | AF15
1 | VBAT | Power
2 | PC13 | I/O |  |  |  |  |  |  |  |  |  |  |  |  |  |  |  |  |  | EVENTOUT
3 | PC14-OSC32_IN | I/O |  |  |  |  |  |  |  |  |  |  |  |  |  |  |  |  |  | EVENTOUT
4 | PC15-OSC32_OUT | I/O |  |  |  |  |  |  |  |  |  |  |  |  |  |  |  |  |  | EVENTOUT
5 | PH0 - OSC_IN | I/O |  |  |  |  |  |  |  |  |  |  |  |  |  |  |  |  |  | EVENTOUT
6 | PH1 - OSC_OUT | I/O |  |  |  |  |  |  |  |  |  |  |  |  |  |  |  |  |  | EVENTOUT
7 | NRST | Reset
8 | VSSA | Power
9 | VDDA | Power
10 | PA0 | I/O | ADC1_IN0 |  |  | TIM2_CH1/TIM2_ETR | TIM5_CH1 | TIM8_ETR |  |  |  | USART2_CTS | UART4_TX |  |  |  |  |  |  | EVENTOUT
11 | PA1 | I/O | ADC1_IN1 |  |  | TIM2_CH2 | TIM5_CH2 |  |  | I2S4_SD/SPI4_MOSI |  | USART2_RTS | UART4_RX |  |  |  |  |  |  | EVENTOUT
12 | PA2 | I/O | ADC1_IN2 |  |  | TIM2_CH3 | TIM5_CH3 | TIM9_CH1 |  | I2S_CKIN |  | USART2_TX |  |  |  |  |  |  |  | EVENTOUT
13 | PA3 | I/O | ADC1_IN3 |  |  | TIM2_CH4 | TIM5_CH4 | TIM9_CH2 |  | I2S2_MCK |  | USART2_RX |  |  | SAI1_SD_B |  |  |  |  | EVENTOUT
14 | PA4 | I/O | DAC_OUT1 ADC1_IN4 |  |  |  |  |  |  | I2S1_WS/SPI1_NSS | I2S3_WS/SPI3_NSS | USART2_CK | DFSDM1_DATIN1 |  |  |  |  |  |  | EVENTOUT
15 | PA5 | I/O | DAC_OUT2 ADC1_IN5 |  |  | TIM2_CH1/TIM2_ETR |  | TIM8_CH1N |  | I2S1_CK/SPI1_SCK |  |  | DFSDM1_CKIN1 |  |  |  |  |  |  | EVENTOUT
16 | PA6 | I/O | ADC1_IN6 |  |  | TIM1_BKIN | TIM3_CH1 | TIM8_BKIN |  | SPI1_MISO | I2S2_MCK | DFSDM2_CKIN1 |  | TIM13_CH1 |  |  | SDIO_CMD |  |  | EVENTOUT
17 | PA7 | I/O | ADC1_IN7 |  |  | TIM1_CH1N | TIM3_CH2 | TIM8_CH1N |  | I2S1_SD/SPI1_MOSI |  | DFSDM2_DATIN1 |  | TIM14_CH1 |  |  |  |  |  | EVENTOUT
18 | PB0 | I/O | ADC1_IN8 |  |  | TIM1_CH2N | TIM3_CH3 | TIM8_CH2N |  |  | I2S5_CK/SPI5_SCK |  |  |  |  |  |  |  |  | EVENTOUT
19 | PB1 | I/O | ADC1_IN9 |  |  | TIM1_CH3N | TIM3_CH4 | TIM8_CH3N |  |  | I2S5_WS/SPI5_NSS |  | DFSDM1_DATIN0 |  |  |  |  |  |  | EVENTOUT
20 | PB2 | I/O |  |  |  | LPTIM1_OUT |  |  |  |  | DFSDM1_CKIN0 |  |  |  |  |  |  |  |  | EVENTOUT
21 | PB10 | I/O |  |  |  | TIM2_CH3 |  |  | I2C2_SCL | I2S2_CK/SPI2_SCK | I2S3_MCK |  |  | FMPI2C1_SCL | DFSDM2_CKOUT |  | SDIO_D7 |  |  | EVENTOUT
22 | VCAP_1 | Power
23 | VSS | Power
24 | VDD | Power
25 | PB12 | I/O |  |  |  | TIM1_BKIN |  |  | I2C2_SMBA | I2S2_WS/I2S3_CK/SPI2_NSS | I2S4_WS/SPI4_NSS | SPI3_SCK |  | CAN2_RX | DFSDM1_DATIN1 | UART5_RX |  |  |  | EVENTOUT
26 | PB13 | I/O |  |  |  | TIM1_CH1N |  |  | FMPI2C1_SMBA | I2S2_CK/SPI2_SCK | I2S4_CK/SPI4_SCK |  |  | CAN2_TX | DFSDM1_CKIN1 | UART5_TX |  |  |  | EVENTOUT
27 | PB14 | I/O |  |  |  | TIM1_CH2N |  | TIM8_CH2N | FMPI2C1_SDA | SPI2_MISO | I2S2_ext_SD |  | DFSDM1_DATIN2 | TIM12_CH1 |  |  | SDIO_D6 |  |  | EVENTOUT
28 | PB15 | I/O |  |  | RTC_REFIN | TIM1_CH3N |  | TIM8_CH3N | FMPI2C1_SCL | I2S2_SD/SPI2_MOSI |  |  | DFSDM1_CKIN2 | TIM12_CH2 |  |  | SDIO_CK |  |  | EVENTOUT
29 | PA8 | I/O |  |  | RCC_MCO_1 | TIM1_CH1 |  |  | I2C3_SCL |  | DFSDM1_CKOUT | USART1_CK | UART7_RX |  | USB_OTG_FS_SOF | CAN3_RX | SDIO_D1 |  |  | EVENTOUT
30 | PA9 | I/O |  |  |  | TIM1_CH2 |  | DFSDM2_CKIN3 | I2C3_SMBA | I2S2_CK/SPI2_SCK |  | USART1_TX |  |  | USB_OTG_FS_VBUS |  | SDIO_D2 |  |  | EVENTOUT
31 | PA10 | Output | GPIO_Output |  |  | TIM1_CH3 |  | DFSDM2_DATIN3 |  | I2S2_SD/SPI2_MOSI | I2S5_SD/SPI5_MOSI | USART1_RX |  |  | USB_OTG_FS_ID |  |  |  |  | EVENTOUT
32 | PA11 | I/O | CAN1_RX |  |  | TIM1_CH4 |  | DFSDM2_CKIN5 |  | I2S2_WS/SPI2_NSS | SPI4_MISO | USART1_CTS | USART6_TX | CAN1_RX | USB_OTG_FS_DM | UART4_RX |  |  |  | EVENTOUT
33 | PA12 | I/O | CAN1_TX |  |  | TIM1_ETR |  | DFSDM2_DATIN5 |  | SPI2_MISO | SPI5_MISO | USART1_RTS | USART6_RX | CAN1_TX | USB_OTG_FS_DP | UART4_TX |  |  |  | EVENTOUT
34 | PA13 | I/O | SYS_JTMS-SWDIO |  | SYS_JTMS-SWDIO |  |  |  |  |  |  |  |  |  |  |  |  |  |  | EVENTOUT
35 | VSS | Power
36 | VDD | Power
37 | PA14 | I/O | SYS_JTCK-SWCLK |  | SYS_JTCK-SWCLK |  |  |  |  |  |  |  |  |  |  |  |  |  |  | EVENTOUT
38 | PA15 | I/O |  |  | SYS_JTDI | TIM2_CH1/TIM2_ETR |  |  |  | I2S1_WS/SPI1_NSS | I2S3_WS/SPI3_NSS | USART1_TX | UART7_TX |  | SAI1_MCLK_A | CAN3_TX |  |  |  | EVENTOUT
39 | PB3 | I/O |  |  | SYS_JTDO-SWO | TIM2_CH2 |  |  | FMPI2C1_SDA | I2S1_CK/SPI1_SCK | I2S3_CK/SPI3_SCK | USART1_RX | UART7_RX | I2C2_SDA | SAI1_SD_A | CAN3_RX |  |  |  | EVENTOUT
40 | PB4 | I/O |  |  | SYS_JTRST |  | TIM3_CH1 |  |  | I2S3_ext_SD/SPI1_MISO | SPI3_MISO |  | UART7_TX | I2C3_SDA | SAI1_SCK_A | CAN3_TX | SDIO_D0 |  |  | EVENTOUT
41 | PB5 | I/O |  |  |  | LPTIM1_IN1 | TIM3_CH2 |  | I2C1_SMBA | I2S1_SD/SPI1_MOSI | I2S3_SD/SPI3_MOSI |  |  | CAN2_RX | SAI1_FS_A | UART5_RX | SDIO_D3 |  |  | EVENTOUT
42 | PB6 | I/O |  |  |  | LPTIM1_ETR | TIM4_CH1 |  | I2C1_SCL |  | DFSDM2_CKIN7 | USART1_TX |  | CAN2_TX |  | UART5_TX | SDIO_D0 |  |  | EVENTOUT
43 | PB7 | I/O |  |  |  | LPTIM1_IN2 | TIM4_CH2 |  | I2C1_SDA |  | DFSDM2_DATIN7 | USART1_RX |  |  |  |  |  |  |  | EVENTOUT
44 | BOOT0 | Boot
45 | PB8 | I/O |  |  |  | LPTIM1_OUT | TIM4_CH3 | TIM10_CH1 | I2C1_SCL |  | I2S5_SD/SPI5_MOSI | DFSDM2_CKIN1 | CAN1_RX | I2C3_SDA |  | UART5_RX | SDIO_D4 |  |  | EVENTOUT
46 | PB9 | I/O |  |  |  |  | TIM4_CH4 | TIM11_CH1 | I2C1_SDA | I2S2_WS/SPI2_NSS | DFSDM2_DATIN1 |  | CAN1_TX | I2C2_SDA |  | UART5_TX | SDIO_D5 |  |  | EVENTOUT
47 | VSS | Power
48 | VDD | Power

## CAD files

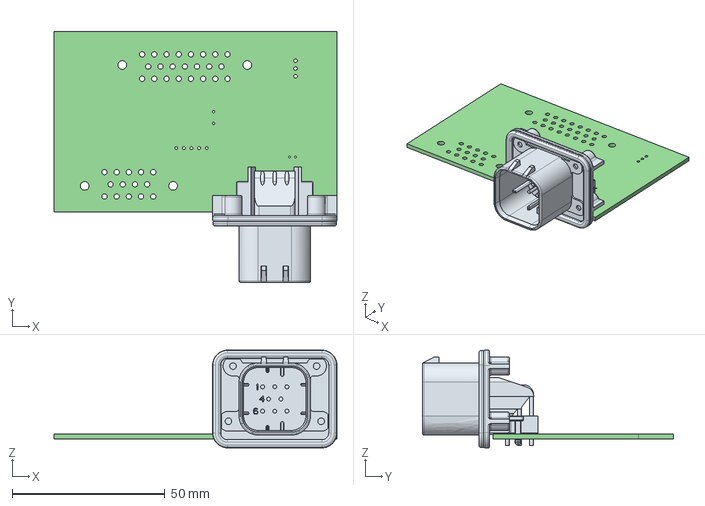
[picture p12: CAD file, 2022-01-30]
DCB/driver-control-board/Model/driver-control-board.step
92.8 x 82.3 x 32.1 mm
driver-control-board PCB

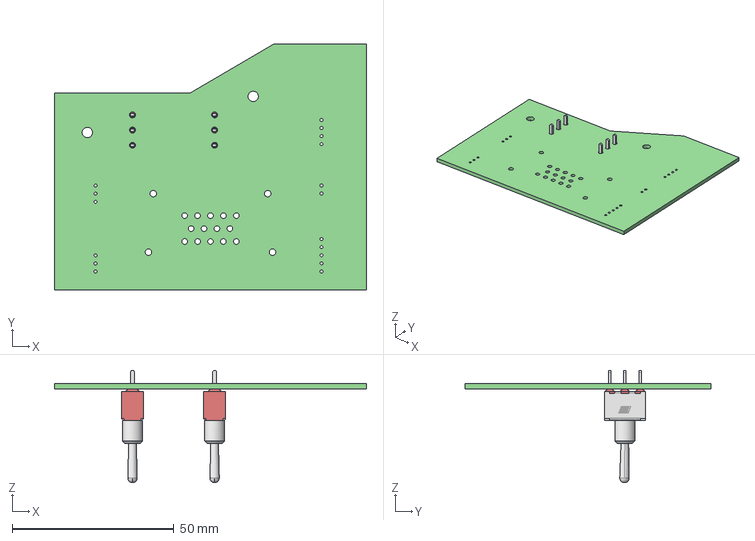
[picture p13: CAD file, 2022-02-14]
DCB/interface-board/Model/interface-board.step
96.5 x 76.2 x 34.8 mm
interface-board PCB

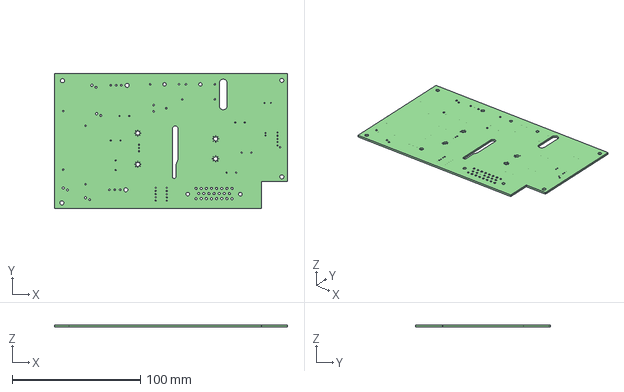
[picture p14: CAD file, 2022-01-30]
HVB/high-voltage-board/Model/high-voltage-board.step
181.6 x 105.4 x 1.60 mm

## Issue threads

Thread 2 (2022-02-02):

updating Driver Interface with 5mmled

uvmaeroshopcomputers, 2022-02-02:
@Cgrund23 Board needs to have 5mm led instead of the SMD led

Cgrund23, 2022-02-03:
Fixed smd Led now 5mm

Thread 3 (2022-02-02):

BMS passthrough board update

uvmaeroshopcomputers, 2022-02-02:
BMS passthrough needs to be re-worked to include extra connectors. See Colin for information

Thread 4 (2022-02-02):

update emrax with connectors

uvmaeroshopcomputers, 2022-02-02:
Connector should be an ampseal on one side and a six pin and two pin on the other. Also, figure out how to run 5V

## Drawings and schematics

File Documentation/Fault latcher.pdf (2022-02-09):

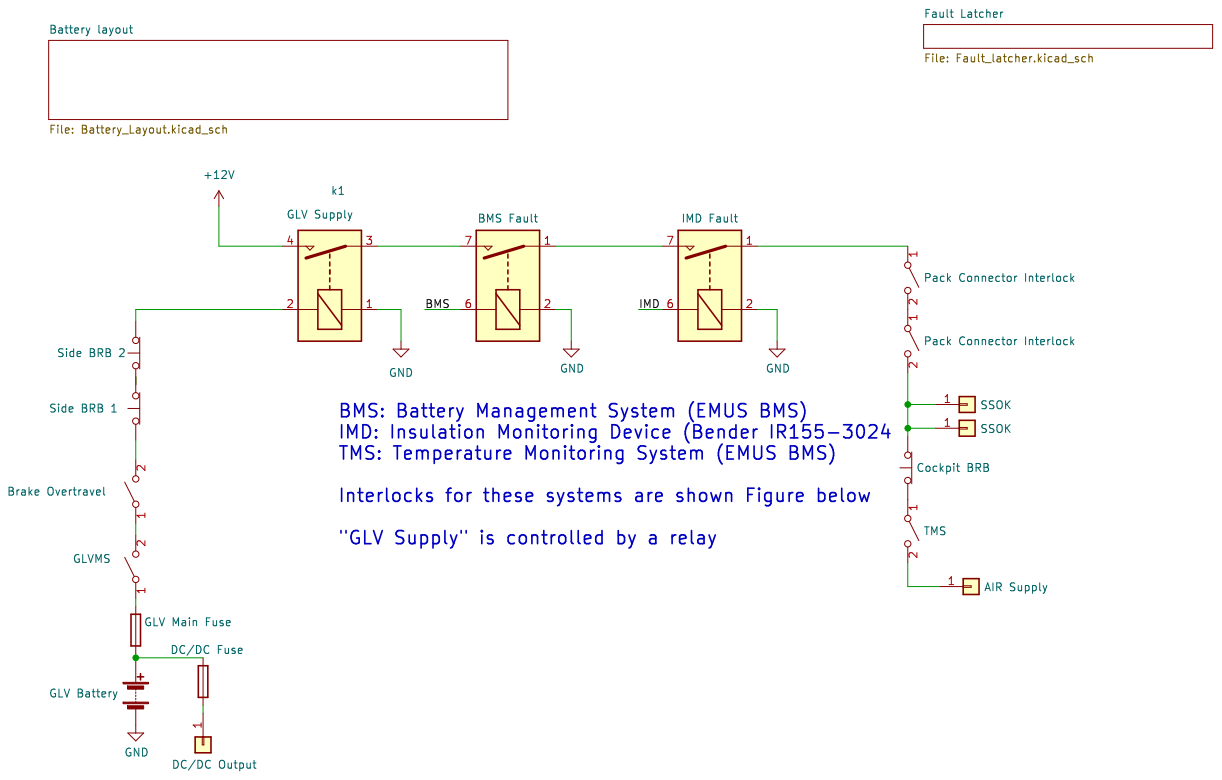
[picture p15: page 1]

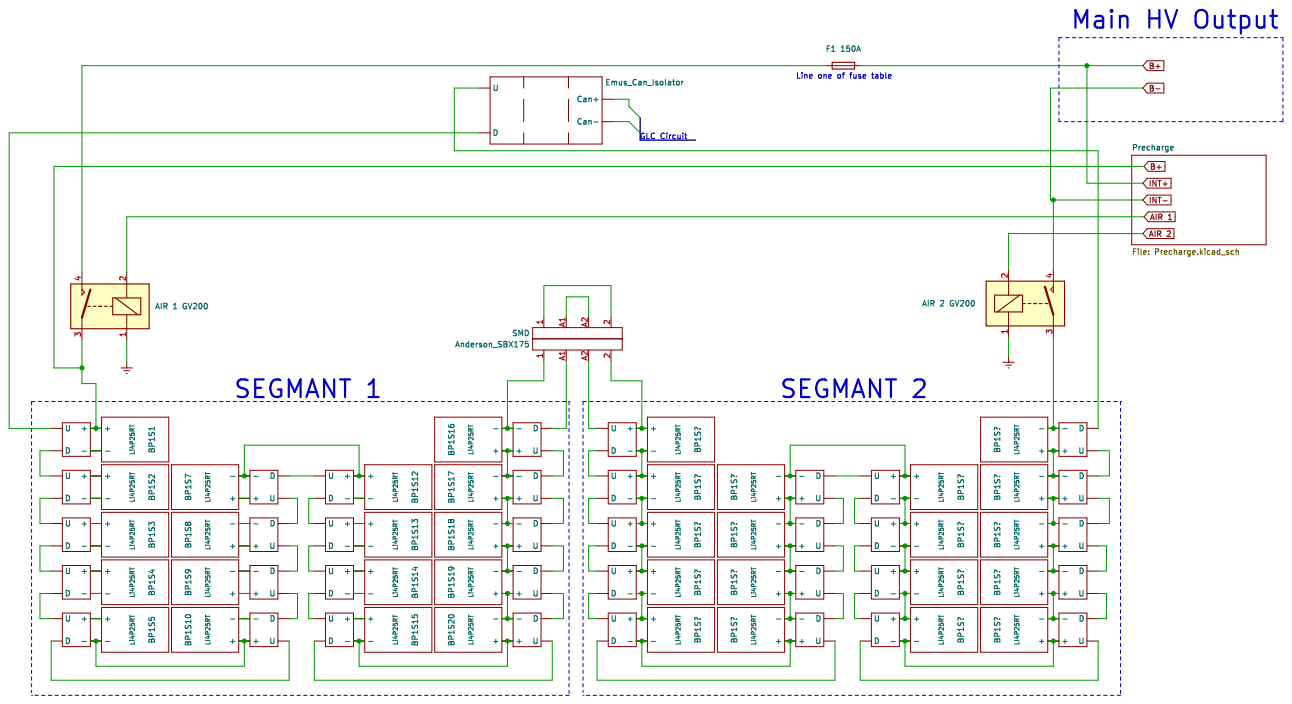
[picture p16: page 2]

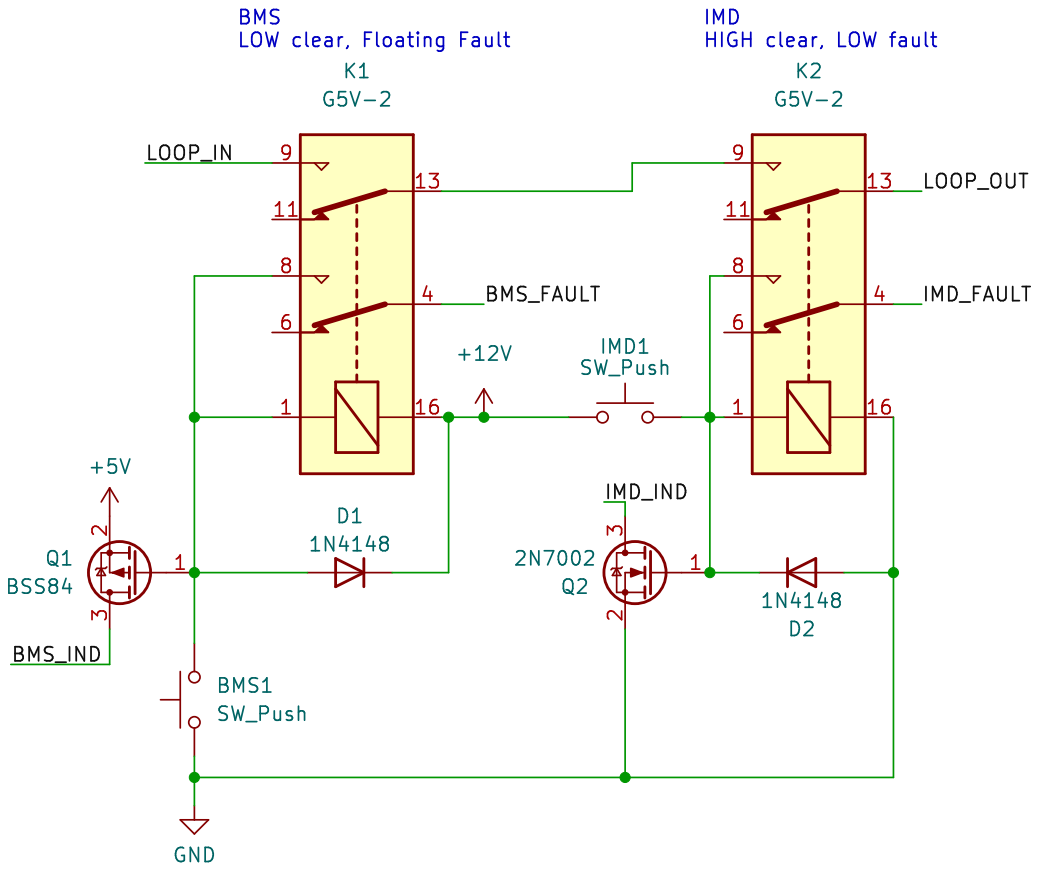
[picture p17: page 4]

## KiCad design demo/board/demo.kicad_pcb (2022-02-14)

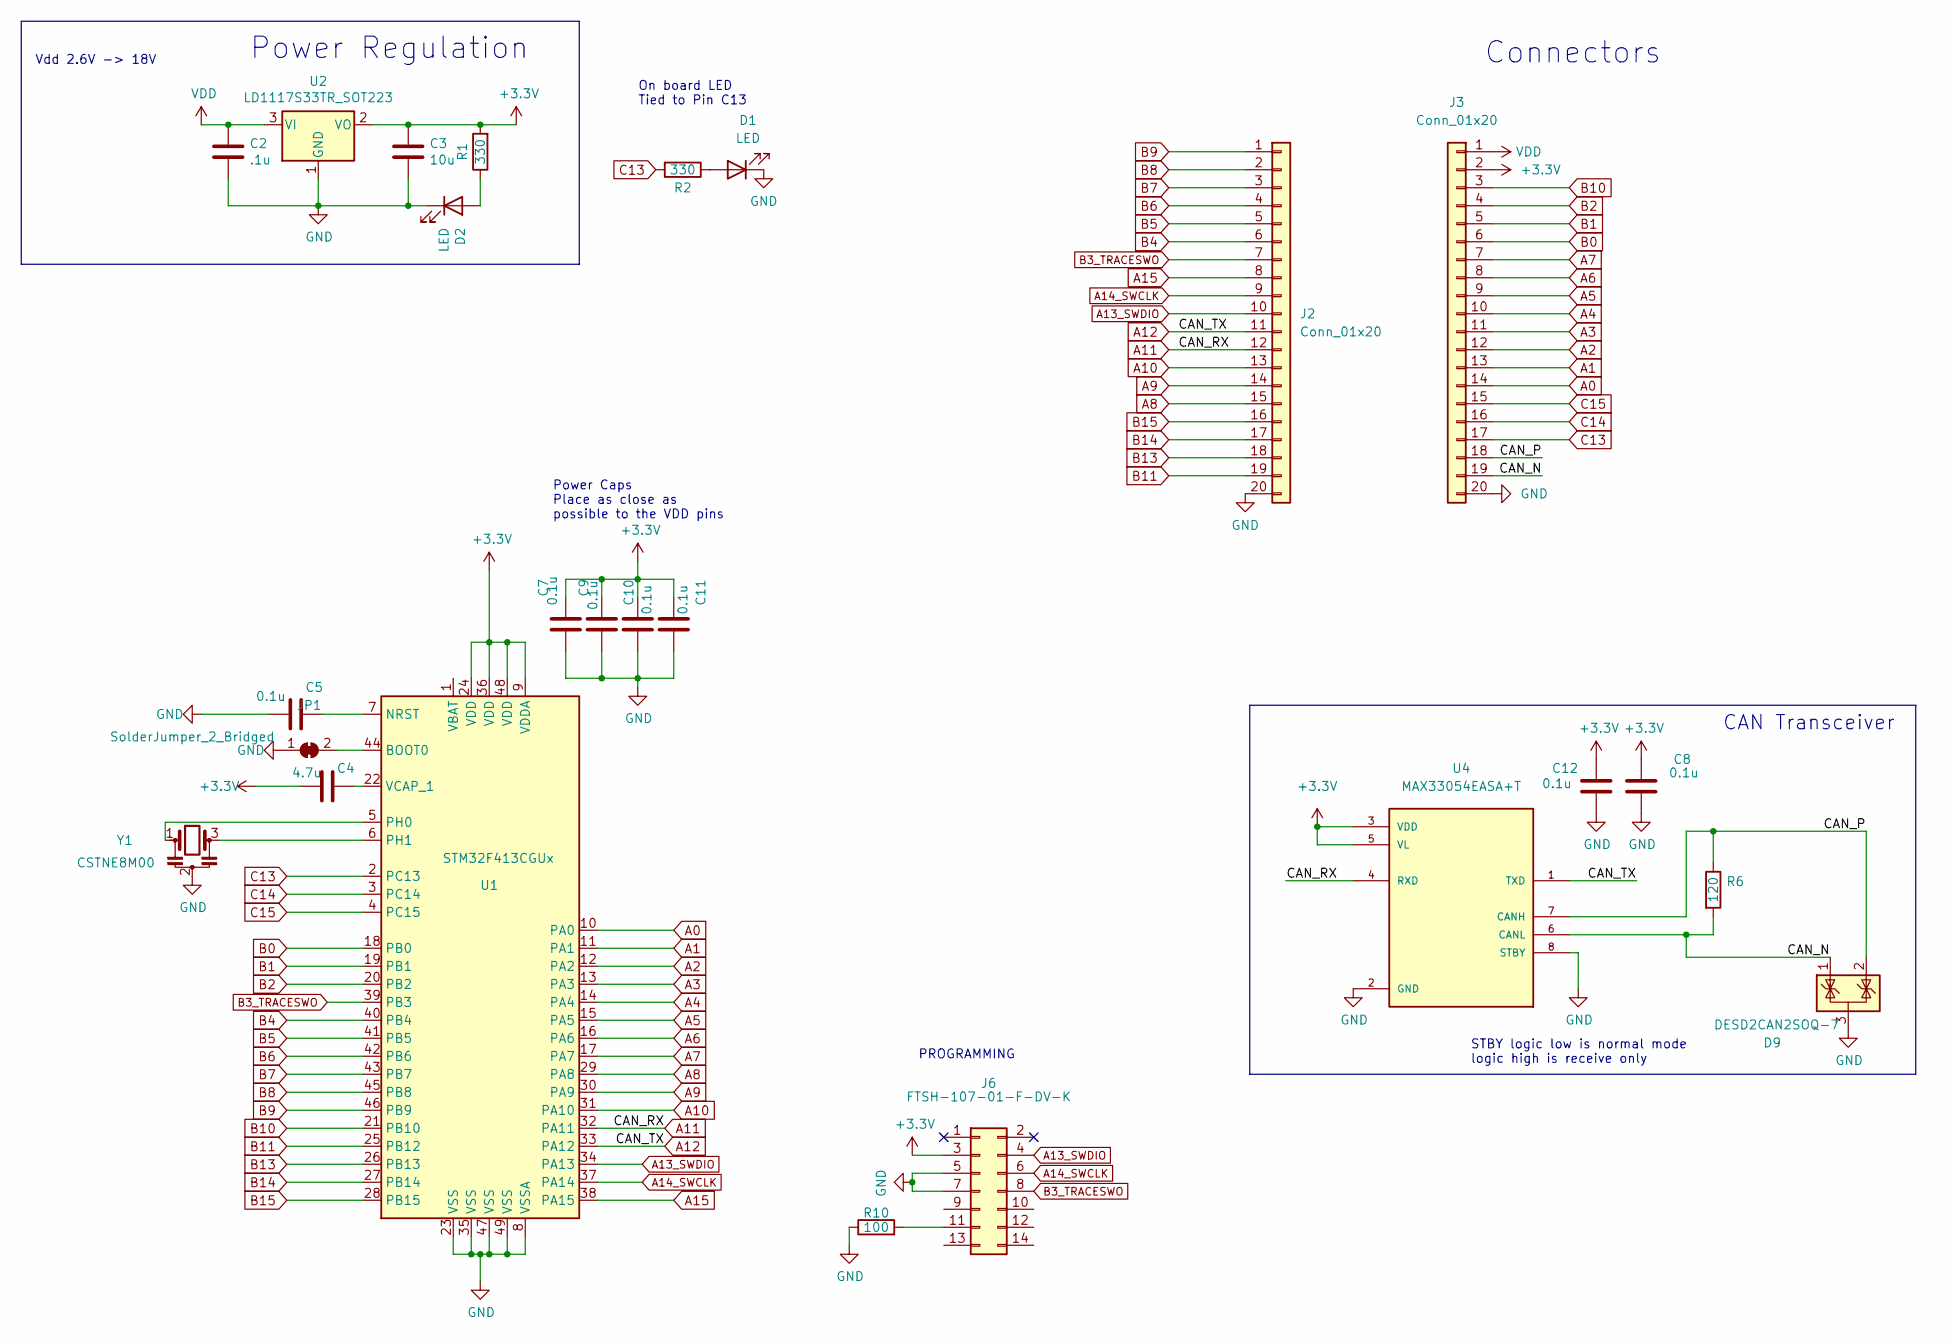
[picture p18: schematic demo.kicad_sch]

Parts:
C2: .1u; C_0603_1608Metric_Pad1.08x0.95mm_HandSolder
C3: 10u; C_0603_1608Metric_Pad1.08x0.95mm_HandSolder
C4: 4.7u; C_0603_1608Metric_Pad1.08x0.95mm_HandSolder
C5, C7, C8, C9, C10, C11, C12: 0.1u; C_0603_1608Metric_Pad1.08x0.95mm_HandSolder
D1, D2: LED; LED_0603_1608Metric_Pad1.05x0.95mm_HandSolder
D9: DESD2CAN2SOQ-7; SOT-23
J2, J3: Conn_01x20; PinHeader_1x20_P2.54mm_Vertical
J6: FTSH-107-01-F-DV-K; PinHeader_2x07_P1.27mm_Vertical_SMD
JP1: SolderJumper_2_Bridged; SolderJumper-2_P1.3mm_Bridged_RoundedPad1.0x1.5mm
R1, R2: 330; R_0603_1608Metric_Pad0.98x0.95mm_HandSolder
R6: 120; R_0603_1608Metric_Pad0.98x0.95mm_HandSolder
R10: 100; R_0603_1608Metric_Pad0.98x0.95mm_HandSolder
U1: STM32F413CGUx; QFN-48-1EP_7x7mm_P0.5mm_EP5.6x5.6mm
U2: LD1117S33TR_SOT223; SOT-223-3_TabPin2
U4: MAX33054EASA+T; SOIC127P600X175-8N
Y1: CSTNE8M00; Resonator_SMD_muRata_CSTxExxV-3Pin_3.0x1.1mm_HandSoldering

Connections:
+3V3: C3.1, C4.2, C7.1, C8.1, C9.1, C10.1, C11.1, C12.1, J3.2, J6.3, R1.2, U1.9 (VDDA), U1.24 (VDD), U1.36 (VDD), U1.48 (VDD), U2.2 (VO), U4.3 (VDD), U4.5 (VL)
/CAN_N: D9.1 (K), J3.19, R6.2, U4.6 (CANL)
/CAN_P: D9.2 (K), J3.18, R6.1, U4.7 (CANH)
A0: J3.14, U1.10 (PA0)
A1: J3.13, U1.11 (PA1)
A2: J3.12, U1.12 (PA2)
A3: J3.11, U1.13 (PA3)
A4: J3.10, U1.14 (PA4)
A5: J3.9, U1.15 (PA5)
A6: J3.8, U1.16 (PA6)
A7: J3.7, U1.17 (PA7)
A8: J2.15, U1.29 (PA8)
A9: J2.14, U1.30 (PA9)
A10: J2.13, U1.31 (PA10)
A11: J2.12, U1.32 (PA11), U4.4 (RXD)
A12: J2.11, U1.33 (PA12), U4.1 (TXD)
A13_SWDIO: J2.10, J6.4, U1.34 (PA13)
A14_SWCLK: J2.9, J6.6, U1.37 (PA14)
A15: J2.8, U1.38 (PA15)
B0: J3.6, U1.18 (PB0)
B1: J3.5, U1.19 (PB1)
B2: J3.4, U1.20 (PB2)
B3_TRACESWO: J2.7, J6.8, U1.39 (PB3)
B4: J2.6, U1.40 (PB4)
B5: J2.5, U1.41 (PB5)
B6: J2.4, U1.42 (PB6)
B7: J2.3, U1.43 (PB7)
B8: J2.2, U1.45 (PB8)
B9: J2.1, U1.46 (PB9)
B10: J3.3, U1.21 (PB10)
B11: J2.19, U1.25 (PB12)
B13: J2.18, U1.26 (PB13)
B14: J2.17, U1.27 (PB14)
B15: J2.16, U1.28 (PB15)
C13: J3.17, R2.2, U1.2 (PC13)
C14: J3.16, U1.3 (PC14)
C15: J3.15, U1.4 (PC15)
GND: C2.2, C3.2, C5.2, C7.2, C8.2, C9.2, C10.2, C11.2, C12.2, D1.1 (K), D2.1 (K), D9.3 (A), J2.20, J3.20, J6.5, J6.7, JP1.1 (A), R10.1, U1.8 (VSSA), U1.23 (VSS), U1.35 (VSS), U1.47 (VSS), U1.49 (VSS), U2.1 (GND), U4.2 (GND), U4.8 (STBY), Y1.2
unnamed: C4.1, U1.22 (VCAP_1)
unnamed: C5.1, U1.7 (NRST)
unnamed: D1.2 (A), R2.1
unnamed: D2.2 (A), R1.1
unnamed: J6.11, R10.2
unnamed: U1.5 (PH0), Y1.1
unnamed: U1.6 (PH1), Y1.3
unnamed: JP1.2 (B), U1.44 (BOOT0)
VDD: C2.1, J3.1, U2.3 (VI)

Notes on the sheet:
CAN Transceiver
On board LED Tied to Pin C13
Vdd 2.6V -> 18V
Power Regulation
Connectors
Power Caps Place as close as possible to the VDD pins
STBY logic low is normal mode logic high is receive only
PROGRAMMING

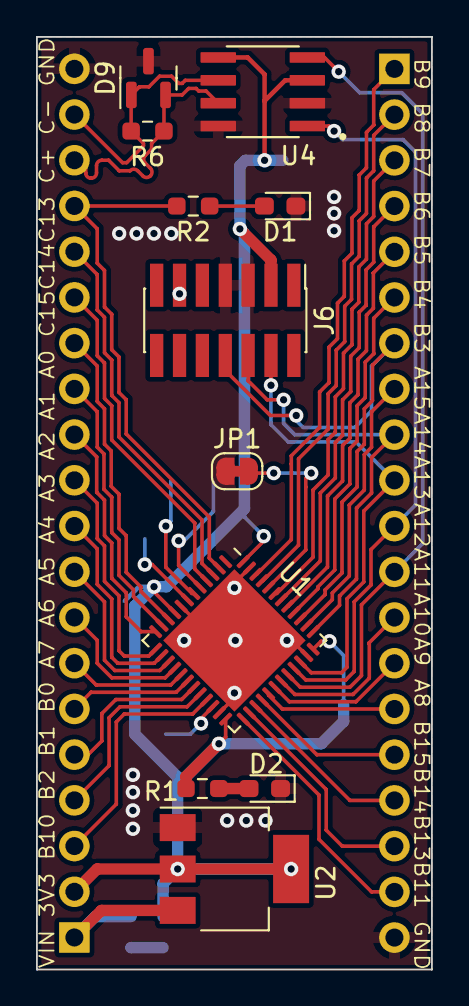
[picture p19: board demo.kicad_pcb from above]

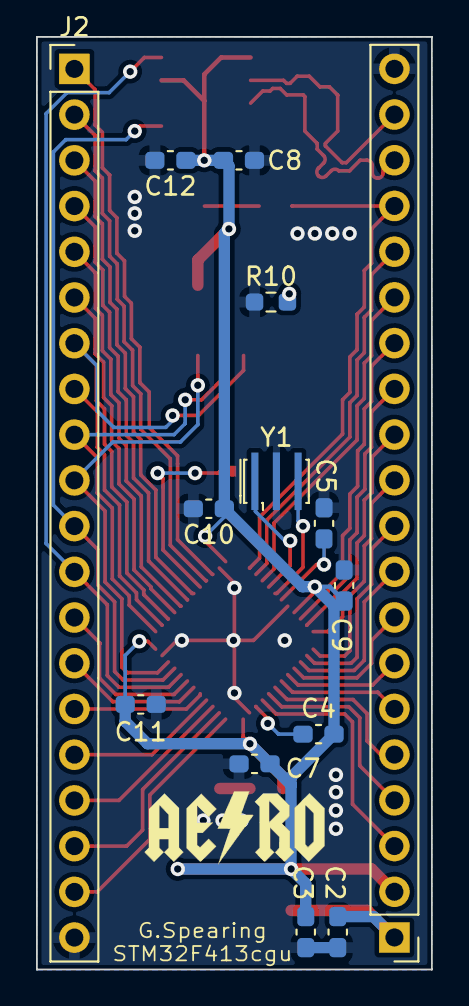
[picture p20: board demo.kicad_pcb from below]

Board: 2 copper layers, 21.9 x 51.8 mm, 25 parts (14 on the bottom side), 47 nets.

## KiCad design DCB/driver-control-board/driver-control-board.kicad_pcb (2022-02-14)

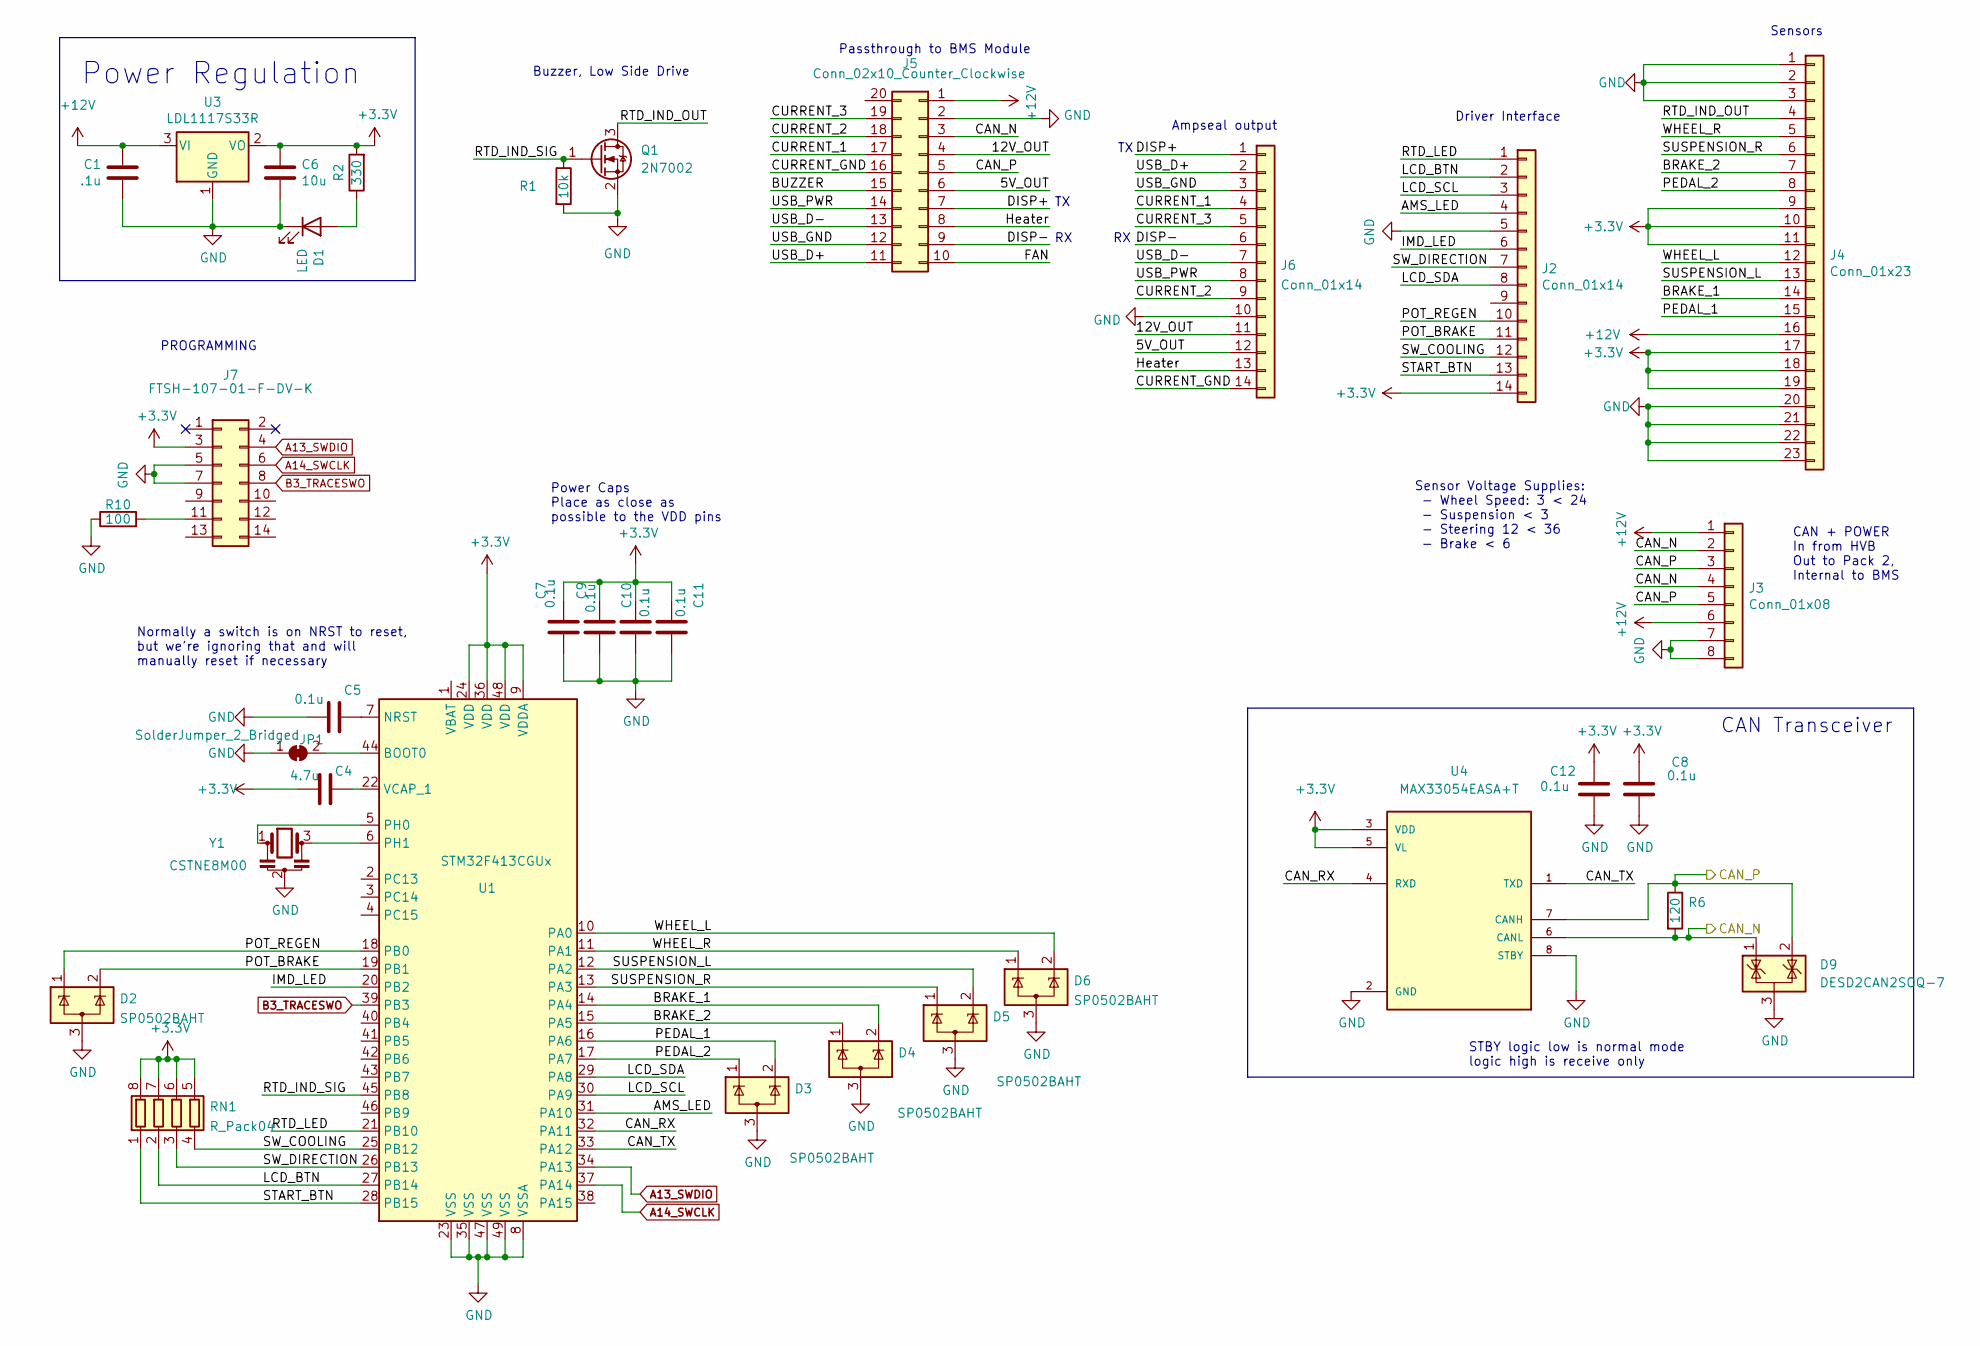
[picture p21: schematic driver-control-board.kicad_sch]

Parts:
C1: .1u; C_0603_1608Metric_Pad1.08x0.95mm_HandSolder
C4: 4.7u; C_0603_1608Metric_Pad1.08x0.95mm_HandSolder
C5, C7, C8, C9, C10, C11, C12: 0.1u; C_0603_1608Metric_Pad1.08x0.95mm_HandSolder
C6: 10u; C_0603_1608Metric_Pad1.08x0.95mm_HandSolder
D1: LED; LED_0603_1608Metric_Pad1.05x0.95mm_HandSolder
D2, D3, D4, D5, D6: SP0502BAHT; SOT-23
D9: DESD2CAN2SOQ-7; SOT-23
J2, J6: Conn_01x14; TE_1-776266-1_14pin_Horizontal
J3: Conn_01x08; TE_1-776280-1_8pin_Horizontal
J4: Conn_01x23; TE_1-770669-1_23pin_Horizontal
J5: Conn_02x10_Counter_Clockwise; PinHeader_2x10_P2.54mm_Horizontal
J7: FTSH-107-01-F-DV-K; PinHeader_2x07_P1.27mm_Vertical_SMD
JP1: SolderJumper_2_Bridged; SolderJumper-2_P1.3mm_Bridged_Pad1.0x1.5mm
Q1: 2N7002; SOT-23
R1: 10k; R_0603_1608Metric_Pad0.98x0.95mm_HandSolder
R2: 330; R_0603_1608Metric_Pad0.98x0.95mm_HandSolder
R6: 120; R_0603_1608Metric_Pad0.98x0.95mm_HandSolder
R10: 100; R_0603_1608Metric_Pad0.98x0.95mm_HandSolder
RN1: R_Pack04; R_Array_Convex_4x1206
U1: STM32F413CGUx; QFN-48-1EP_7x7mm_P0.5mm_EP5.6x5.6mm
U3: LDL1117S33R; SOT-223-3_TabPin2
U4: MAX33054EASA+T; SOIC127P600X175-8N
Y1: CSTNE8M00; Resonator_SMD_muRata_CSTxExxV-3Pin_3.0x1.1mm_HandSoldering

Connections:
+3V3: C4.2, C6.1, C7.1, C8.1, C9.1, C10.1, C11.1, C12.1, J2.14, J4.9, J4.10, J4.11, J4.17, J4.18, J4.19, J7.3, R2.2, RN1.5 (R4.2), RN1.6 (R3.2), RN1.7 (R2.2), RN1.8 (R1.2), U1.9 (VDDA), U1.24 (VDD), U1.36 (VDD), U1.48 (VDD), U3.2 (VO), U4.3 (VDD), U4.5 (VL)
+12V: C1.1, J3.1, J3.6, J4.16, J5.1, U3.3 (VI)
/5V_OUT: J5.6, J6.12
/12V_OUT: J5.4, J6.11
/AMS_LED: J2.4, U1.31 (PA10)
/BRAKE_1: D4.2 (K), J4.14, U1.14 (PA4)
/BRAKE_2: D4.1 (K), J4.7, U1.15 (PA5)
/BUZZER: J5.15
/CAN_N: D9.1 (K), J3.2, J3.4, J5.3, R6.2, U4.6 (CANL)
/CAN_P: D9.2 (K), J3.3, J3.5, J5.5, R6.1, U4.7 (CANH)
/CAN_RX: U1.32 (PA11), U4.4 (RXD)
/CAN_TX: U1.33 (PA12), U4.1 (TXD)
/CURRENT_1: J5.17, J6.4
/CURRENT_2: J5.18, J6.9
/CURRENT_3: J5.19, J6.5
/CURRENT_GND: J5.16, J6.14
/DISP+: J5.7, J6.1
/DISP-: J5.9, J6.6
/FAN: J5.10
/Heater: J5.8, J6.13
/IMD_LED: J2.6, U1.20 (PB2)
/LCD_BTN: J2.2, RN1.2 (R2.1), U1.27 (PB14)
/LCD_SCL: J2.3, U1.30 (PA9)
/LCD_SDA: J2.8, U1.29 (PA8)
/PEDAL_1: D3.2 (K), J4.15, U1.16 (PA6)
/PEDAL_2: D3.1 (K), J4.8, U1.17 (PA7)
/POT_BRAKE: D2.2 (K), J2.11, U1.19 (PB1)
/POT_REGEN: D2.1 (K), J2.10, U1.18 (PB0)
/RTD_IND_OUT: J4.4, Q1.3 (D)
/RTD_IND_SIG: Q1.1 (G), R1.1, U1.45 (PB8)
/RTD_LED: J2.1, U1.21 (PB10)
/START_BTN: J2.13, RN1.1 (R1.1), U1.28 (PB15)
/SUSPENSION_L: D5.2 (K), J4.13, U1.12 (PA2)
/SUSPENSION_R: D5.1 (K), J4.6, U1.13 (PA3)
/SW_COOLING: J2.12, RN1.4 (R4.1), U1.25 (PB12)
/SW_DIRECTION: J2.7, RN1.3 (R3.1), U1.26 (PB13)
/USB_D+: J5.11, J6.2
/USB_D-: J5.13, J6.7
/USB_GND: J5.12, J6.3
/USB_PWR: J5.14, J6.8
/WHEEL_L: D6.2 (K), J4.12, U1.10 (PA0)
/WHEEL_R: D6.1 (K), J4.5, U1.11 (PA1)
A13_SWDIO: J7.4, U1.34 (PA13)
A14_SWCLK: J7.6, U1.37 (PA14)
B3_TRACESWO: J7.8, U1.39 (PB3)
GND: C1.2, C5.2, C6.2, C7.2, C8.2, C9.2, C10.2, C11.2, C12.2, D1.1 (K), D2.3 (A), D3.3 (A), D4.3 (A), D5.3 (A), D6.3 (A), D9.3 (A), J2.5, J3.7, J3.8, J4.1, J4.2, J4.3, J4.20, J4.21, J4.22, J4.23, J5.2, J6.10, J7.5, J7.7, JP1.1 (A), Q1.2 (S), R1.2, R10.1, U1.8 (VSSA), U1.23 (VSS), U1.35 (VSS), U1.47 (VSS), U1.49 (VSS), U3.1 (GND), U4.2 (GND), U4.8 (STBY), Y1.2
unnamed: C4.1, U1.22 (VCAP_1)
unnamed: C5.1, U1.7 (NRST)
unnamed: D1.2 (A), R2.1
unnamed: J7.11, R10.2
unnamed: JP1.2 (B), U1.44 (BOOT0)
unnamed: U1.5 (PH0), Y1.1
unnamed: U1.6 (PH1), Y1.3

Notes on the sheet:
Ampseal output
Sensor Voltage Supplies: - Wheel Speed: 3 < 24 - Suspension < 3 - Steering 12 < 36 - Brake < 6
CAN + POWER In from HVB Out to Pack 2, Internal to BMS
CAN Transceiver
Normally a switch is on NRST to reset, but we're ignoring that and will manually reset if necessary
Buzzer, Low Side Drive
Driver Interface
Power Caps Place as close as possible to the VDD pins
Power Regulation
Sensors
STBY logic low is normal mode logic high is receive only
Passthrough to BMS Module
PROGRAMMING

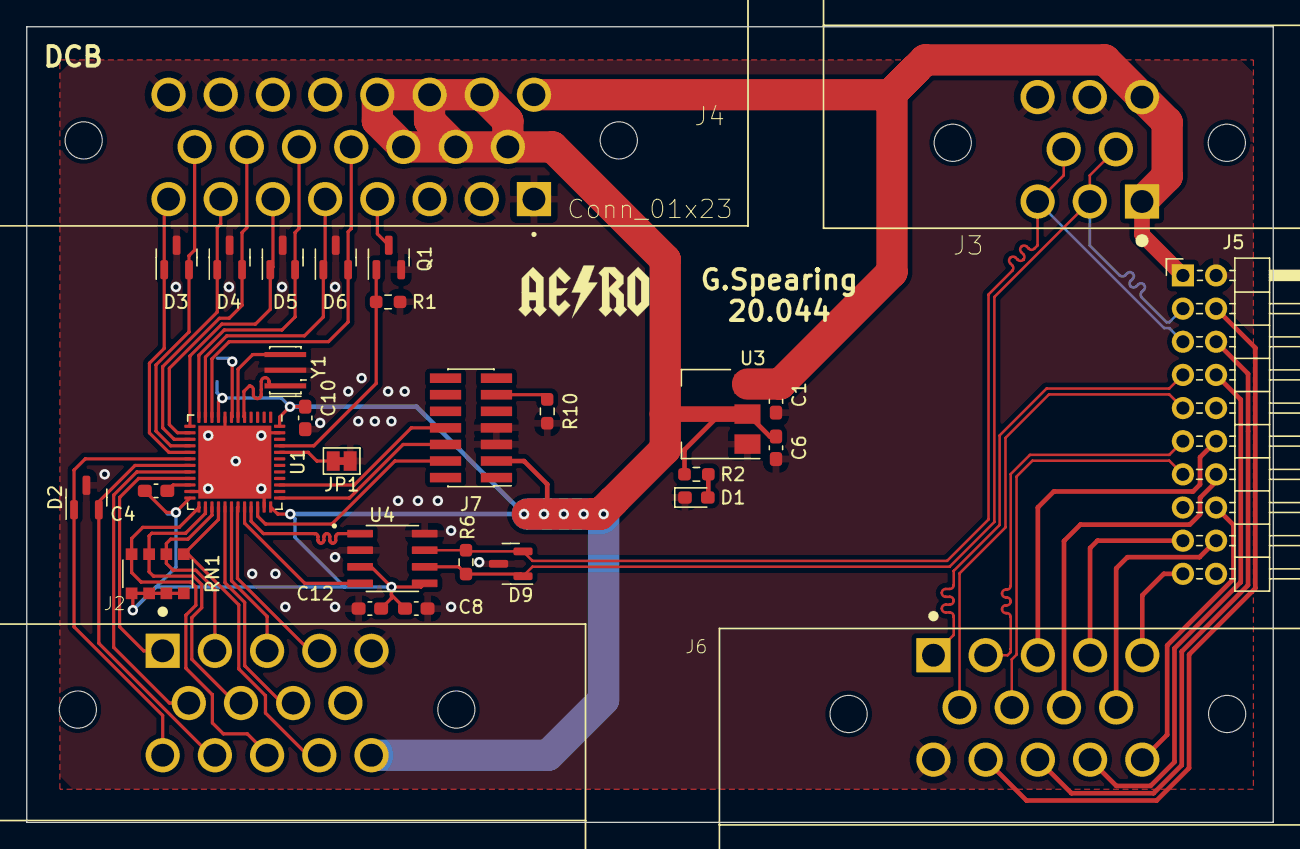
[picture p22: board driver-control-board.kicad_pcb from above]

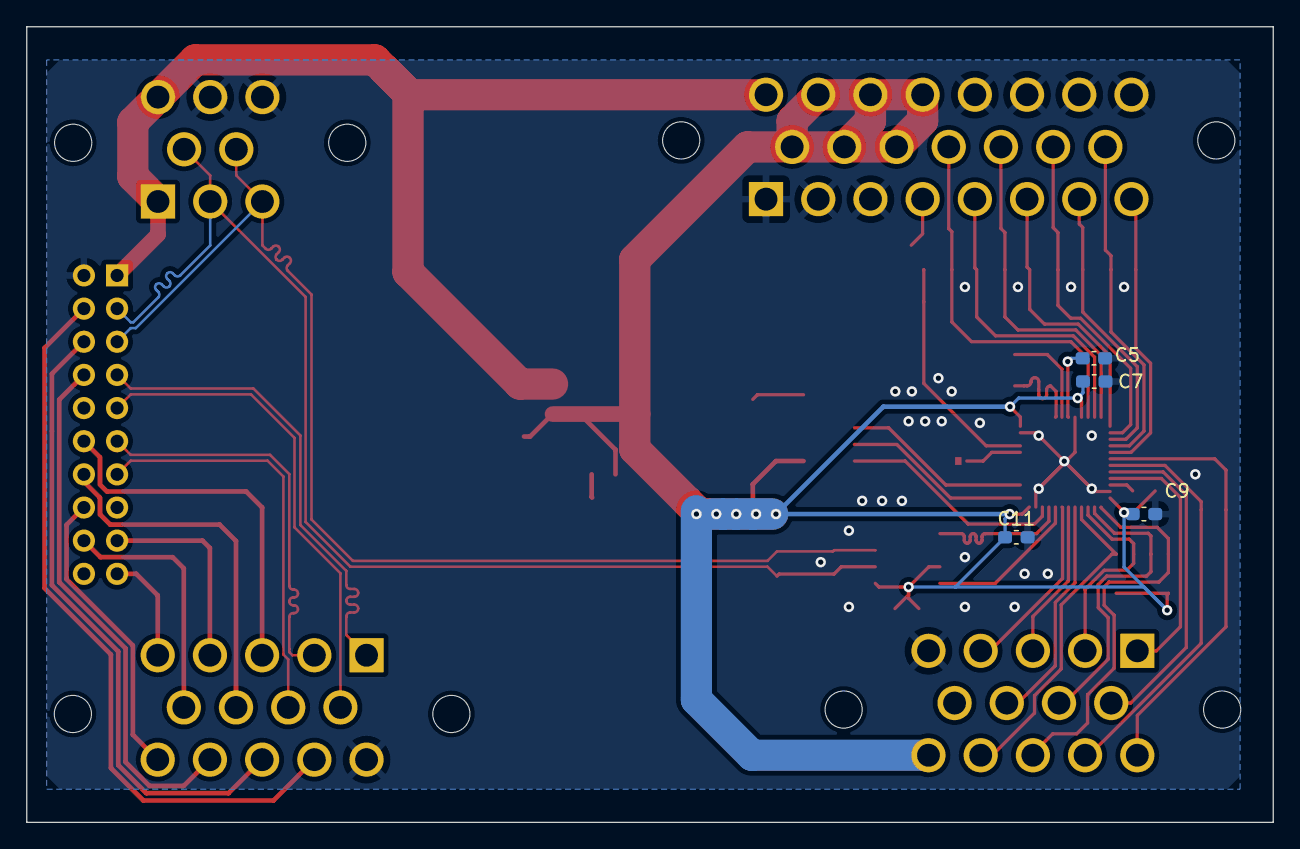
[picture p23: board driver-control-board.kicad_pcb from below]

Board: 2 copper layers, 95.5 x 61.0 mm, 34 parts (4 on the bottom side), 51 nets.

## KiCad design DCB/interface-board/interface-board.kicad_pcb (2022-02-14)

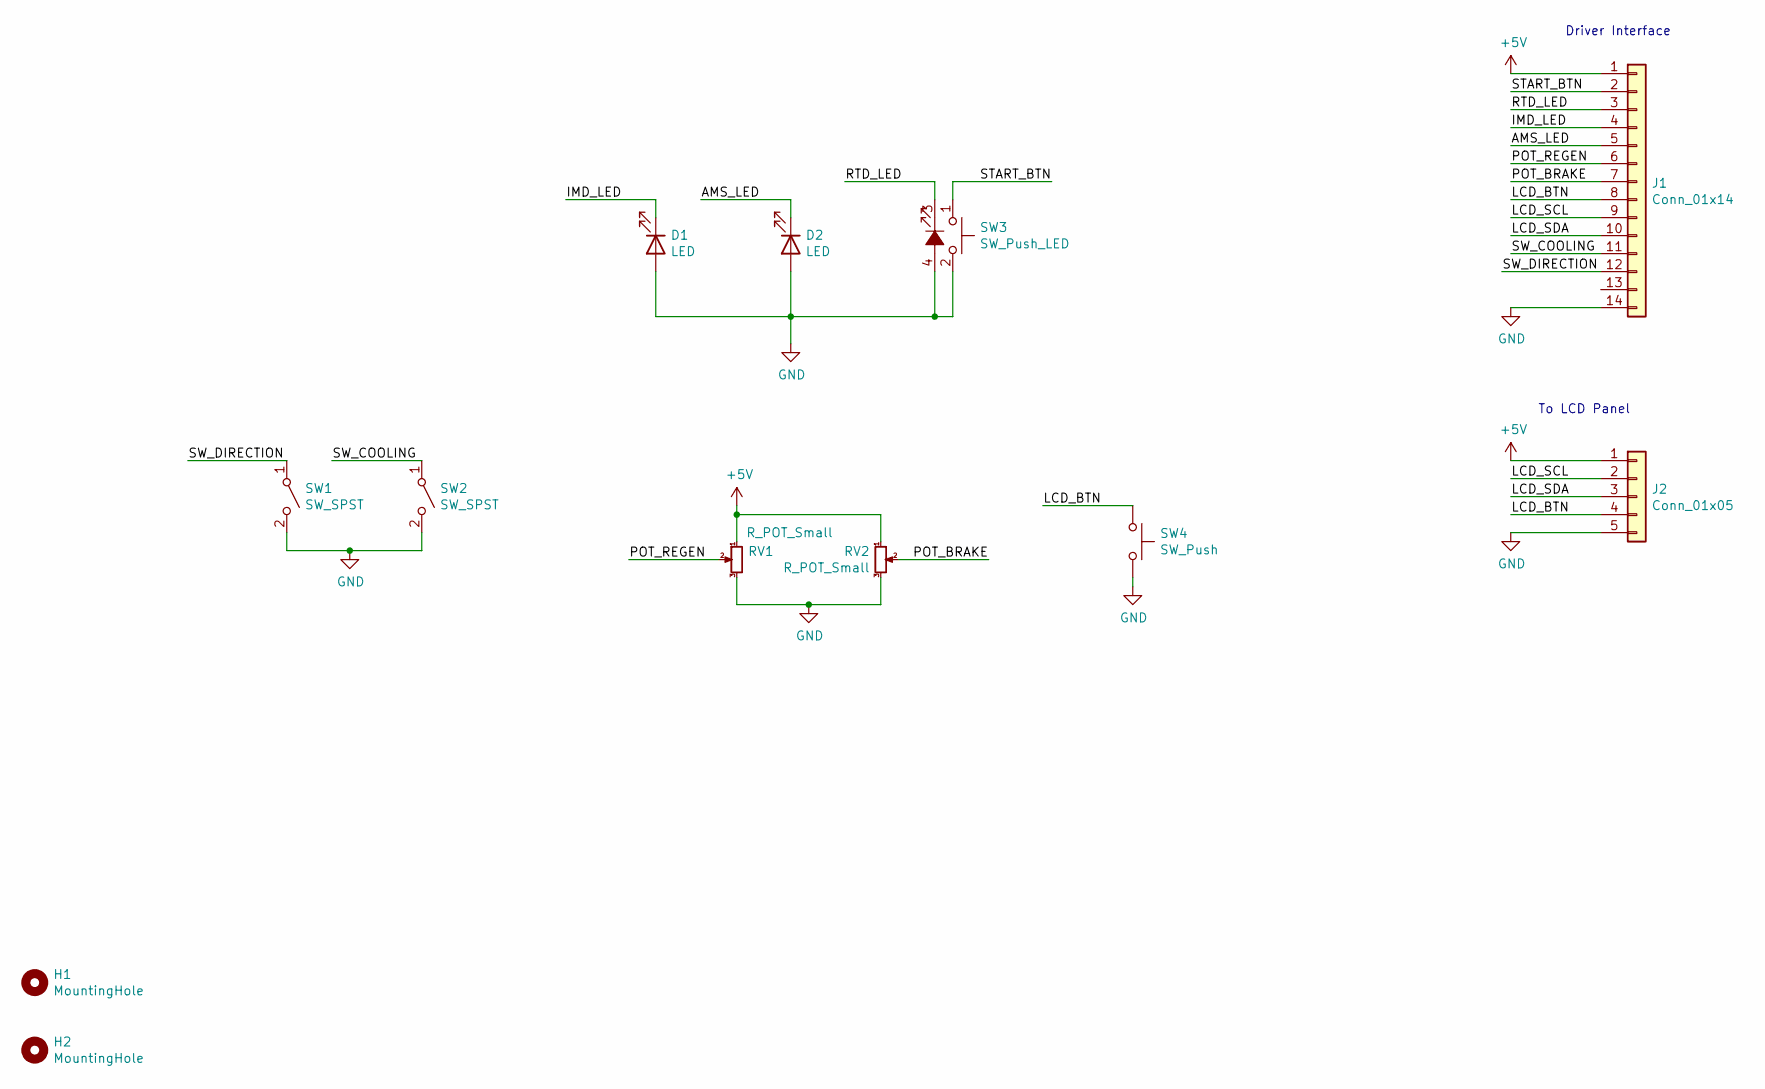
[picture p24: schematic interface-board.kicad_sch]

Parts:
D1, D2: LED; LED_0603_1608Metric_Pad1.05x0.95mm_HandSolder
H1, H2: MountingHole; MountingHole_3.2mm_M3
J1: Conn_01x14; TE_1-776262-1_14pin_Vertical
J2: Conn_01x05; JST_XH_S5B-XH-A-1_1x05_P2.50mm_Horizontal
RV1, RV2: R_POT_Small; JST_XH_S3B-XH-A-1_1x03_P2.50mm_Horizontal
SW1, SW2: SW_SPST; Toggle_Switch_100SP1T1B4M2QE
SW3: SW_Push_LED; JST_XH_S4B-XH-A-1_1x04_P2.50mm_Horizontal
SW4: SW_Push; JST_XH_S2B-XH-A-1_1x02_P2.50mm_Horizontal

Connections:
+5V: J1.1, J2.1, RV1.1, RV2.1
/AMS_LED: D2.1 (K), J1.5
/IMD_LED: D1.1 (K), J1.4
/LCD_BTN: J1.8, J2.4, SW4.1
/LCD_SCL: J1.9, J2.2
/LCD_SDA: J1.10, J2.3
/POT_BRAKE: J1.7, RV2.2
/POT_REGEN: J1.6, RV1.2
/RTD_LED: J1.3, SW3.3 (K)
/START_BTN: J1.2, SW3.1
/SW_COOLING: J1.11, SW2.1 (A)
/SW_DIRECTION: J1.12, SW1.1 (A)
GND: D1.2 (A), D2.2 (A), J1.14, J2.5, RV1.3, RV2.3, SW1.2 (B), SW2.2 (B), SW3.2, SW3.4 (A), SW4.2

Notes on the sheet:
To LCD Panel
Driver Interface

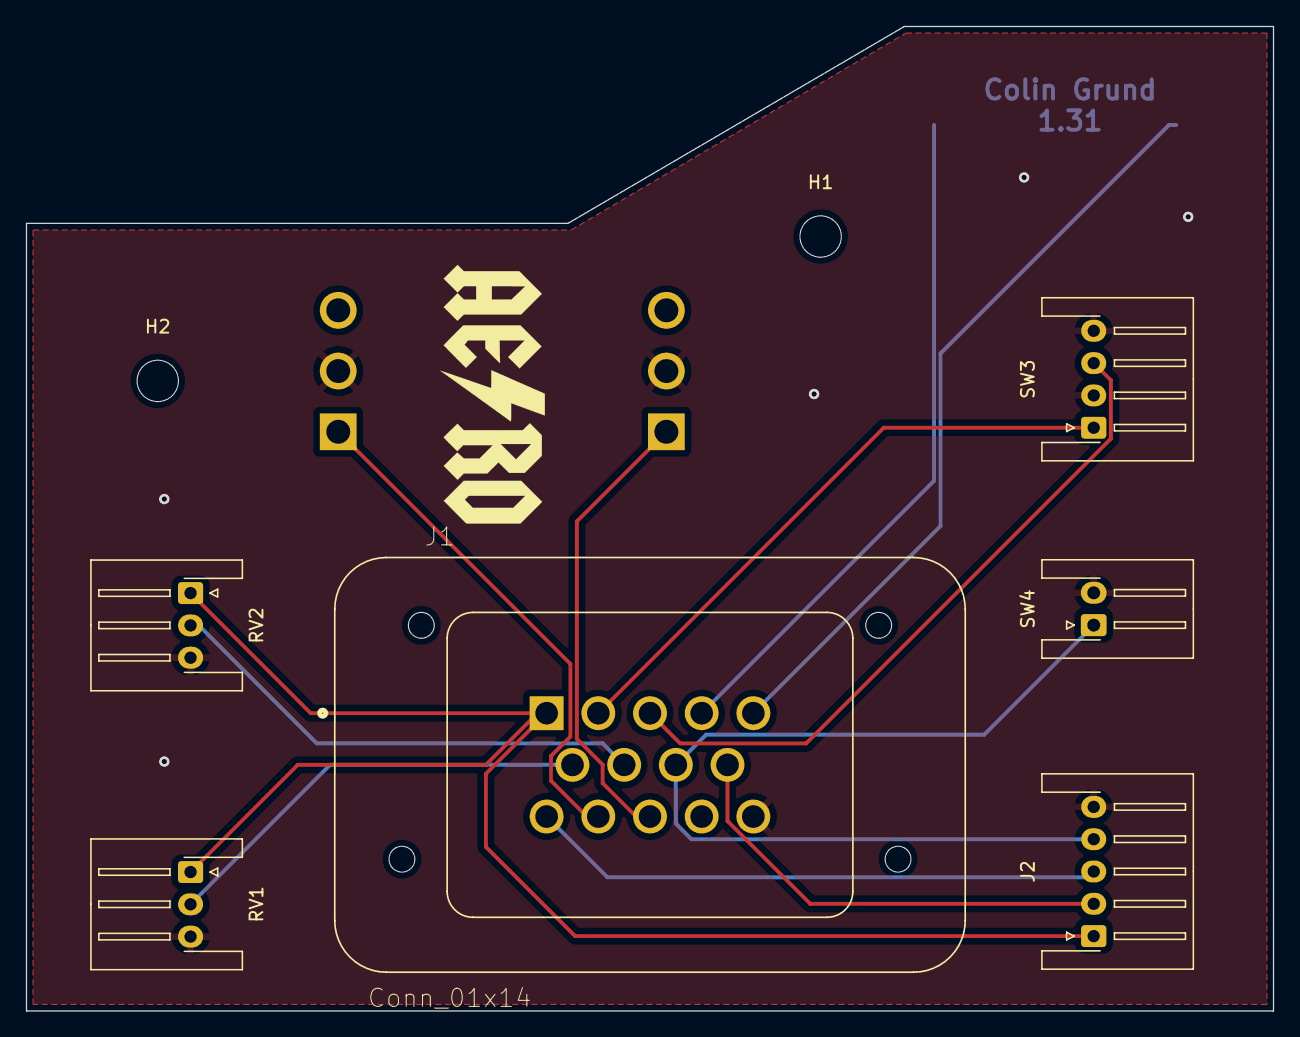
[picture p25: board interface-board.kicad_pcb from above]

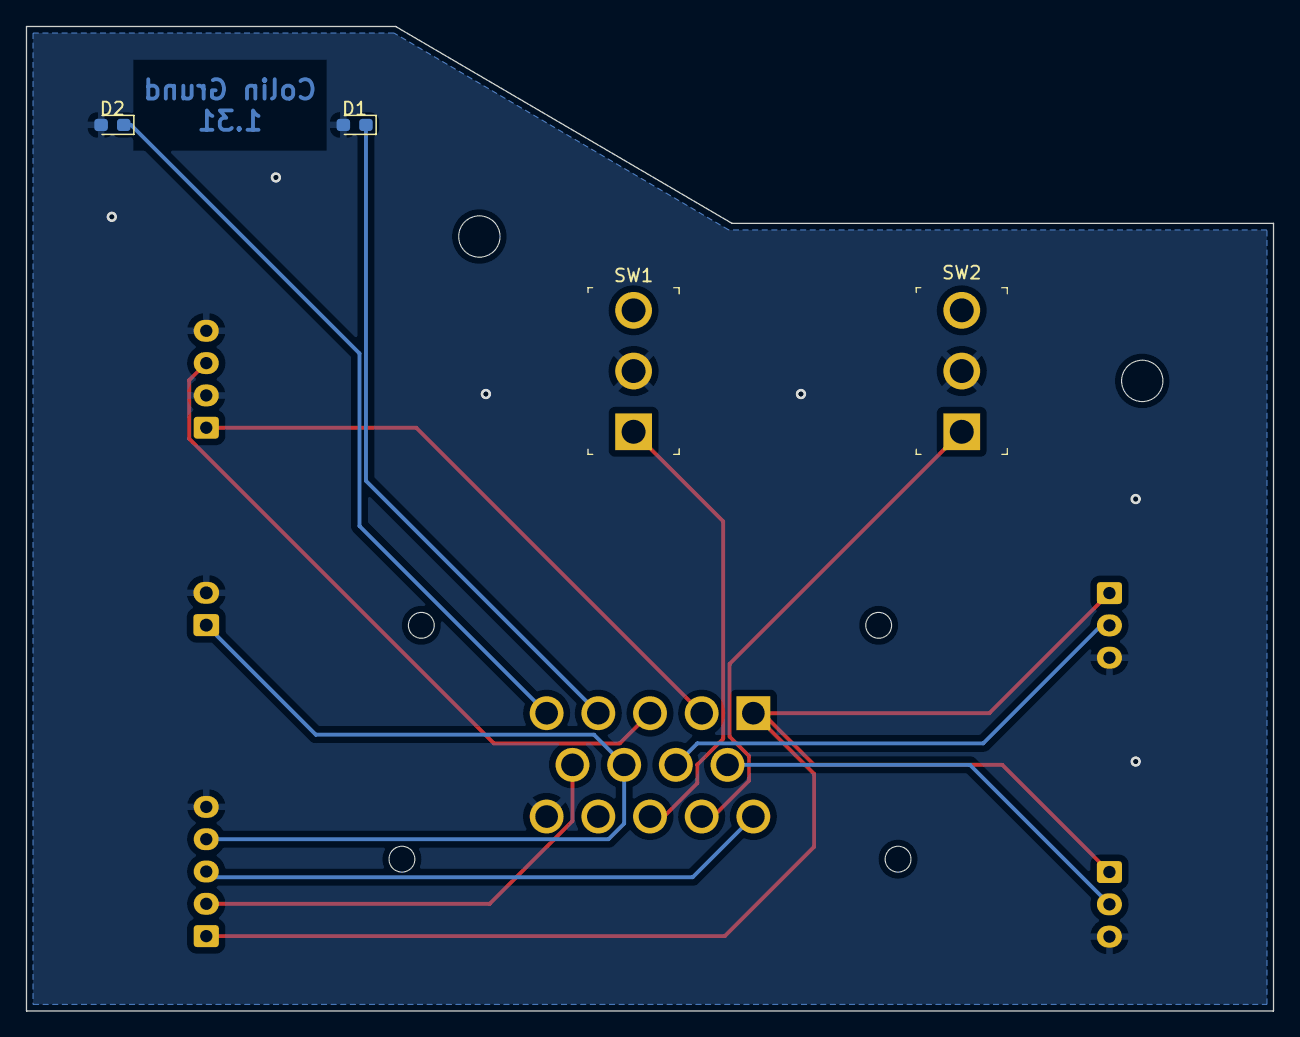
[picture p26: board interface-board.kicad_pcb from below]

Board: 2 copper layers, 96.5 x 76.2 mm, 12 parts (4 on the bottom side), 13 nets.

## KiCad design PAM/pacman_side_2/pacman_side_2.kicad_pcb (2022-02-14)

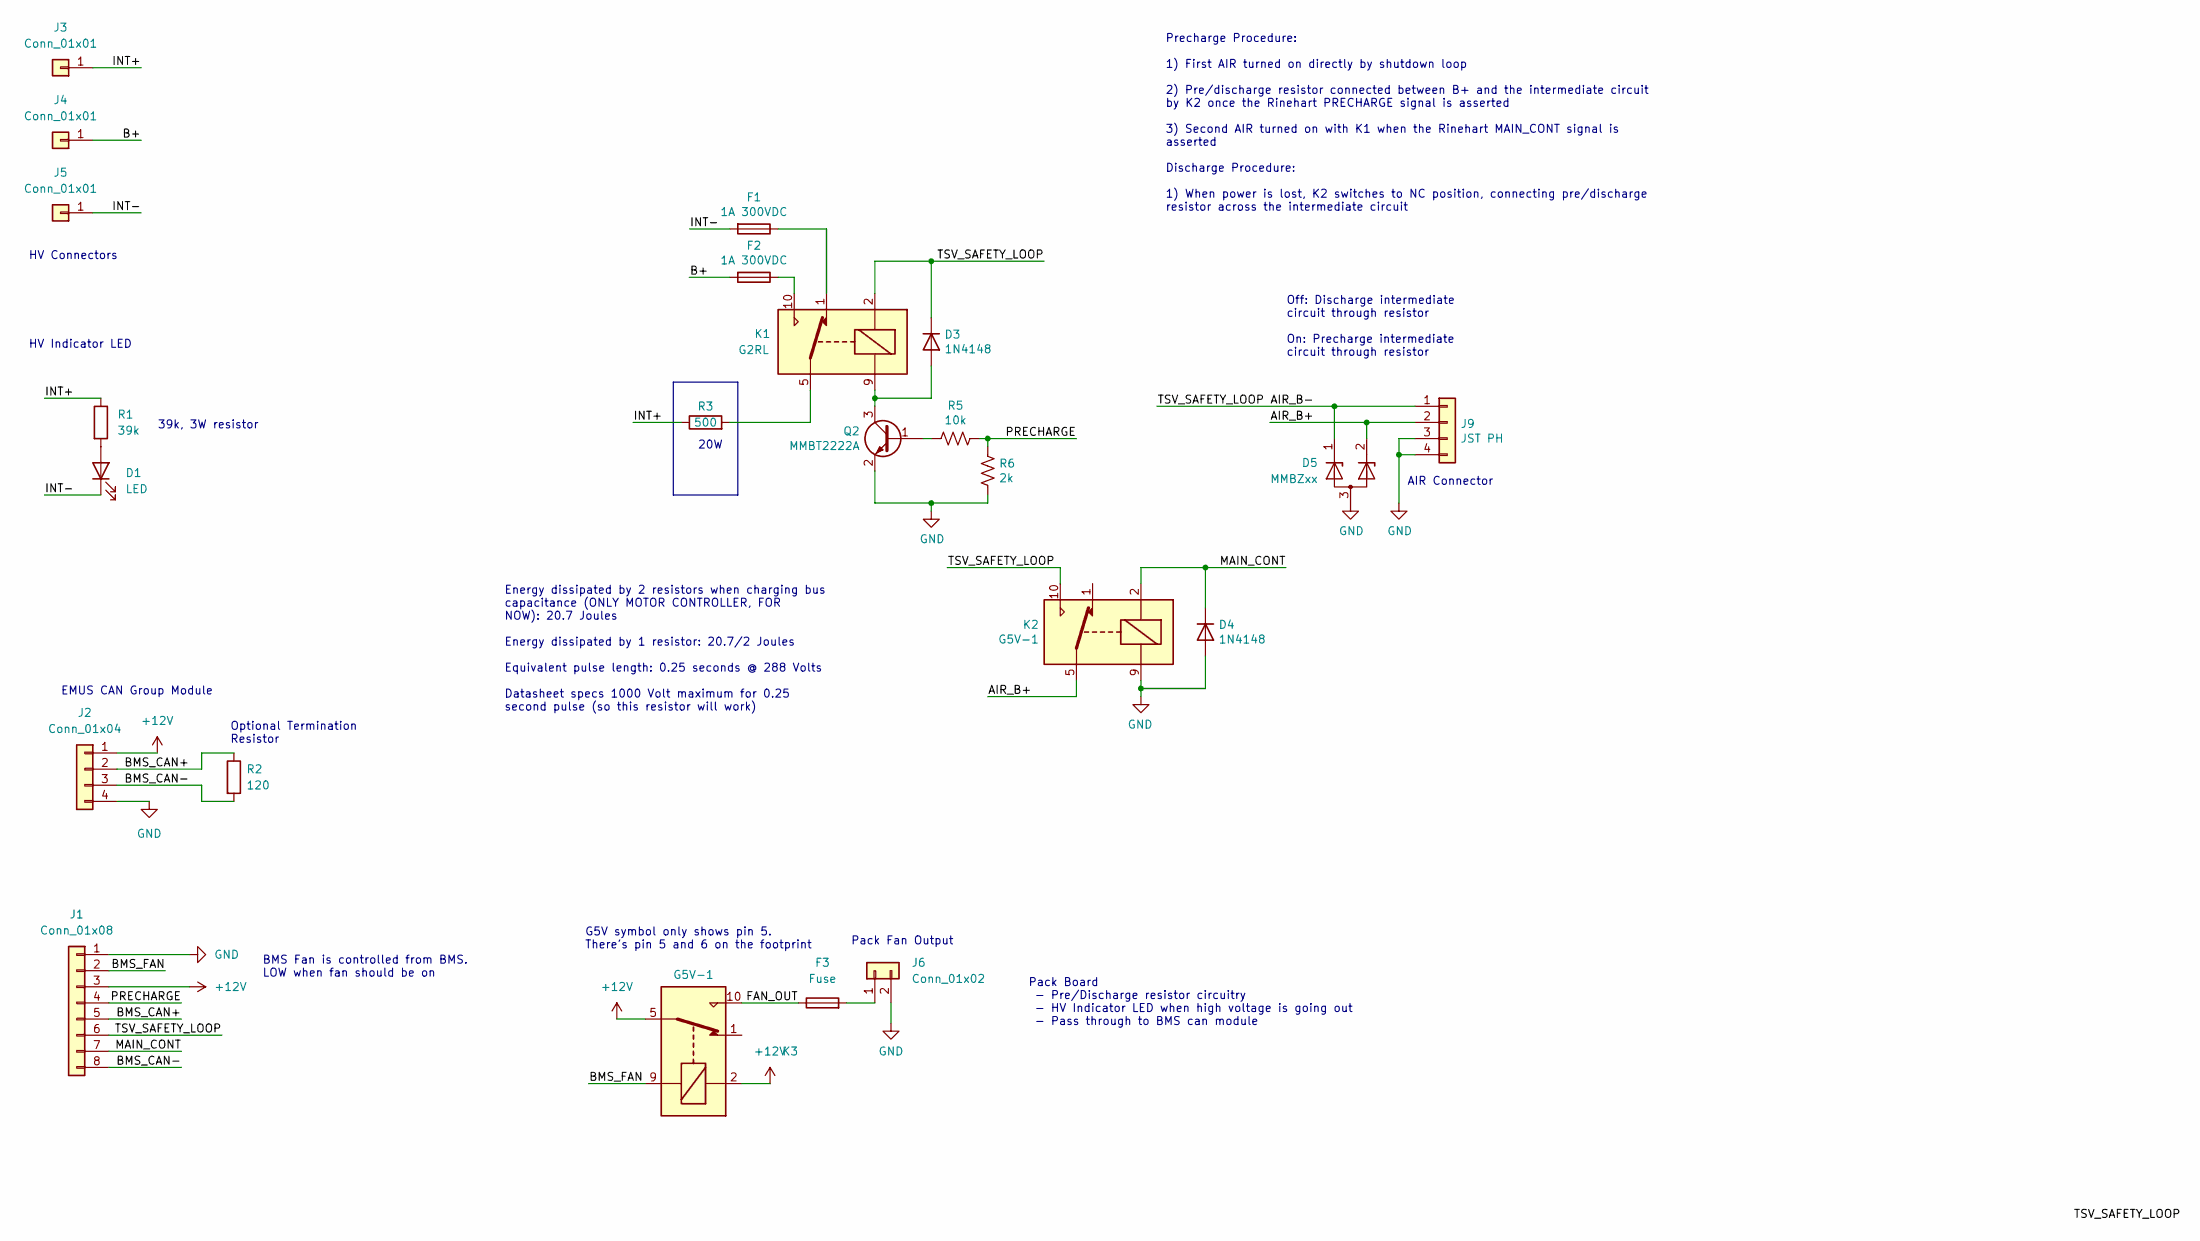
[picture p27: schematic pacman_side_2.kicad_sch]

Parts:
D1: LED; LPA-C011301S-x LED 0805 LIGHT PIPE SINGLE VERT SMD
D3, D4: 1N4148; D_MiniMELF
D5: MMBZxx; SOT-23
F1, F2: 1A 300VDC; Fuseholder_Cylinder-5x20mm_Schurter_0031_8201_Horizontal_Op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
F3: Fuse; Fuseholder_Blade_Mini_Keystone_3568
J1: Conn_01x08; TE_1-776276-1_8pin_Vertical
J2: Conn_01x04; JST_XH_B4B-XH-A_1x04_P2.50mm_Vertical
J3, J4, J5: Conn_01x01; Hirose_DF63M-1P-3.96DSA_1x01_P3.96mm_Vertical
J6: Conn_01x02; JST_XH_B2B-XH-A_1x02_P2.50mm_Vertical
J9: JST PH; JST_PH_B4B-PH-K_1x04_P2.00mm_Vertical
K1: G2RL
K2, K3: G5V-1; Relay_SPDT_Omron_G5V-1
Q2: MMBT2222A; SOT-23
R1: 39k; R_Axial_DIN0414_L11.9mm_D4.5mm_P25.40mm_Horizontal
R2: 120; R_0603_1608Metric_Pad0.98x0.95mm_HandSolder
R3: 500; TO-220-2_Horizontal_TabDown
R5: 10k; R_0603_1608Metric
R6: 2k; R_0603_1608Metric

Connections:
+12V: J1.3, J2.1, K3.2, K3.5, K3.6
/AIR_B+: D5.2 (K), J9.2, K2.5, K2.6
/AIR_B-: D3.1 (K), D5.1 (K), J1.6, J9.1, K1.2, K2.10
/B+: F2.2, J4.1
/BMS_CAN+: J1.5, J2.2, R2.1
/BMS_CAN-: J1.8, J2.3, R2.2
/BMS_FAN: J1.2, K3.9
/FAN_OUT: F3.1, K3.10
/INT+: J3.1, R1.1, R3.1
/INT-: D1.1 (K), F1.2, J5.1
/MAIN_CONT: D4.1 (K), J1.7, K2.2
/PRECHARGE: J1.4, R5.2, R6.2
GND: D4.2 (A), D5.3 (A), J1.1, J2.4, J6.2, J9.3, J9.4, K2.9, Q2.2 (E), R6.1
unnamed: D1.2 (A), R1.2
unnamed: D3.2 (A), K1.9, Q2.3 (C)
unnamed: F1.1, K1.1
unnamed: F2.1, K1.10
unnamed: F3.2, J6.1
unnamed: K1.5, K1.6, R3.2
unnamed: Q2.1 (B), R5.1

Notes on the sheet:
EMUS CAN Group Module
Precharge Procedure: 1) First AIR turned on directly by shutdown loop 2) Pre/discharge resistor connected between B+ and the intermediate circuit by K2 once the Rinehart PRECHARGE signal is asserted 3) Second AIR turned on with K1 when the Rinehart MAIN_CONT signal is asserted Discharge Procedure: 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
AIR Connector
20W
39k, 3W resistor
Pack Fan Output
Energy dissipated by 2 resistors when charging bus capacitance (ONLY MOTOR CONTROLLER, FOR NOW): 20.7 Joules Energy dissipated by 1 resistor: 20.7/2 Joules Equivalent pulse length: 0.25 seconds @ 288 Volts Datasheet specs 1000 Volt maximum for 0.25 second pulse (so this resistor will work)
Optional Termination Resistor
Off: Discharge intermediate circuit through resistor On: Precharge intermediate circuit through resistor
G5V symbol only shows pin 5. There's pin 5 and 6 on the footprint
HV Connectors
BMS Fan is controlled from BMS. LOW when fan should be on
Pack Board - Pre/Discharge resistor circuitry - HV Indicator LED when high voltage is going out - Pass through to BMS can module
HV Indicator LED

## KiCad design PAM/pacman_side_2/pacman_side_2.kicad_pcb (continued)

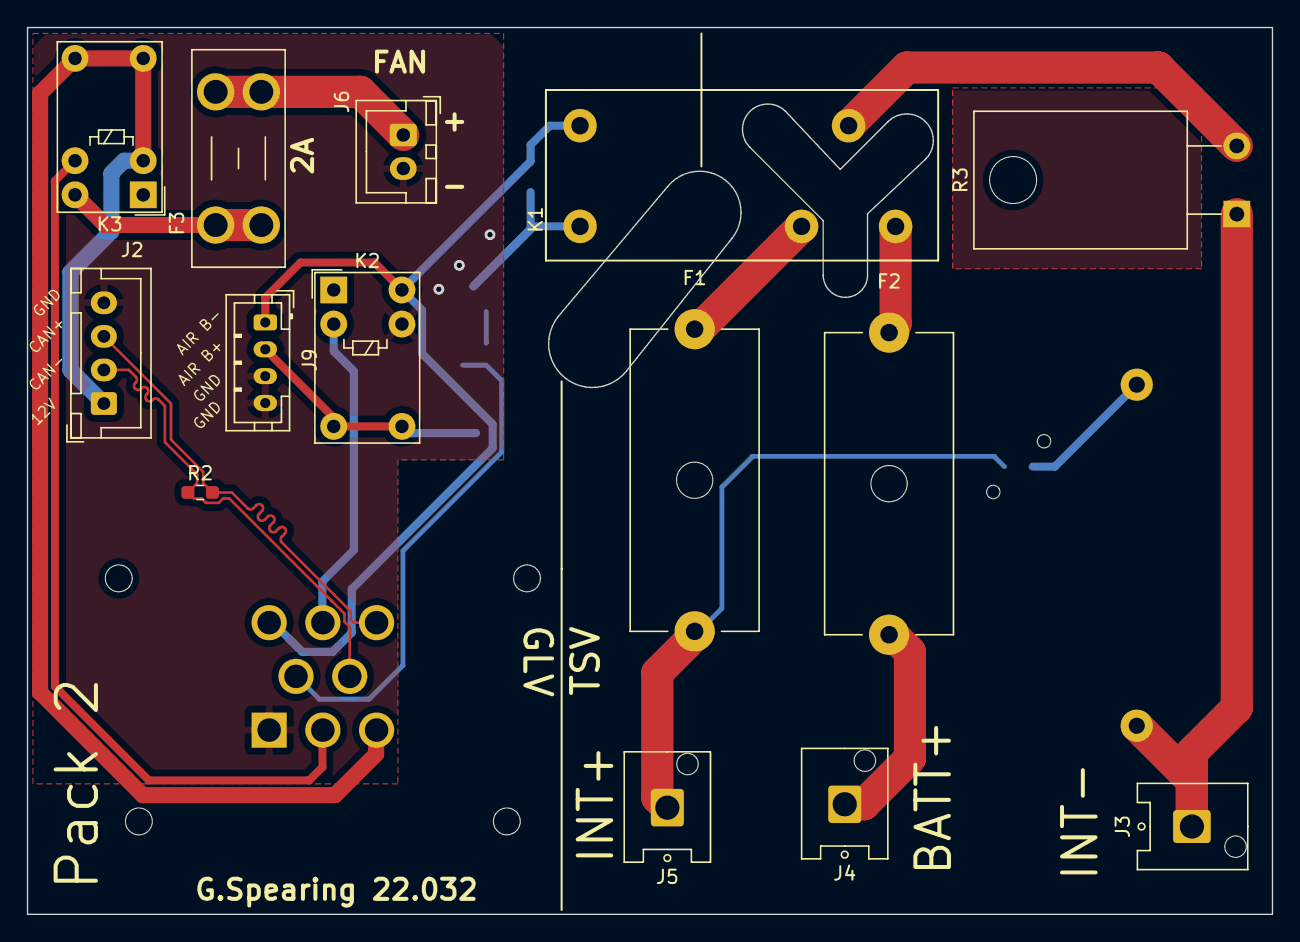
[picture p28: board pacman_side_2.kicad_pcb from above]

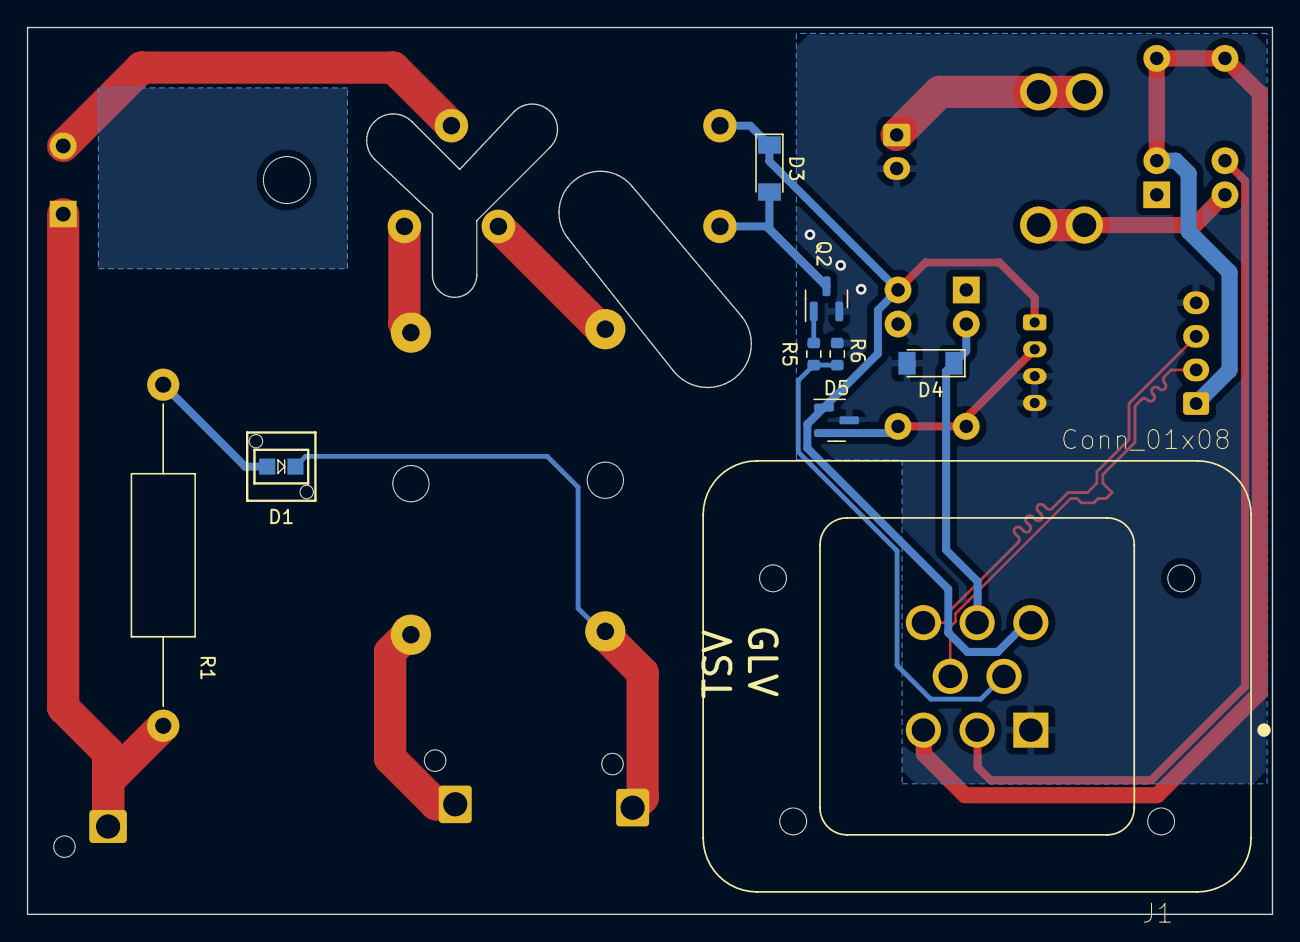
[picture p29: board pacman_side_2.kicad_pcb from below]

Board: 2 copper layers, 92.7 x 66.0 mm, 23 parts (9 on the bottom side), 20 nets.

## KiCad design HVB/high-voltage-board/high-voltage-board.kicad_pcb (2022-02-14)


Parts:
F1: 2A; Fuseholder_Cylinder-5x20mm_Schurter_0031_8201_Horizontal_Op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
F2: 35A; Fuseholder_Cylinder-5x20mm_Schurter_0031_8201_Horizontal_Op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
H1, H2, H3, H4: MountingHole; MountingHole_3.2mm_M3
J1: Conn_01x23; TE_1-770669-1_23pin_Horizontal
J2: HECS; JST_XH_B5B-XH-A_1x05_P2.50mm_Vertical
J3, J8: HV+; Hirose_DF63M-1P-3.96DSA_1x01_P3.96mm_Vertical
J4, J11: HV-; Hirose_DF63M-1P-3.96DSA_1x01_P3.96mm_Vertical
J5: HV+; TE_MATE-N-LOK_1-770870-x_1x03_P4.14mm_Vertical
J6: HV-; TE_MATE-N-LOK_1-770870-x_1x03_P4.14mm_Vertical
J7: Conn_01x02; JST_XH_B2B-XH-A_1x02_P2.50mm_Vertical
J9: Bender-LV; JST_XH_B5B-XH-A_1x05_P2.50mm_Vertical
R9, R10: 10k; R_Axial_Power_L50.0mm_W9.0mm_P60.96mm

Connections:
+3V3: J7.2; also elsewhere on the board
+5VA: J1.10, J2.2
+12V: J1.6, J1.13, J1.20, J9.5; also elsewhere on the board
/CAN+: J1.8, J1.15, J1.23; also elsewhere on the board
/CAN-: J1.7, J1.14, J1.22; also elsewhere on the board
/DCDC_OUT: J1.1, J1.2, J1.3, J1.4; also elsewhere on the board
/HECS_AN1: J1.16, J2.5
/HECS_AN2: J1.9, J2.4
/HECS_AN3: J1.17, J2.3
/IMD_OK: J1.18, J9.4
/TEMP-: J7.1; also elsewhere on the board
/TSAL/HV+: F1.1; also elsewhere on the board
/TSAL_GND: J1.21; also elsewhere on the board
/vicor/HV+: F2.1; also elsewhere on the board
GND: J1.5, J1.11, J1.12, J2.1, J9.1, J9.2, J9.3; also elsewhere on the board
HV+: F1.2, F2.2, J3.1, J5.1, J5.2, J5.3, R9.1
HV-: J4.1, J6.1, J6.2, J6.3, R10.1; also elsewhere on the board
unnamed: J8.1, R9.2
unnamed: J11.1, R10.2

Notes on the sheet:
Global nets connected to this sheet: GND, 12V
Global nets connected to this sheet: 12V, GND
IMD_OK Goes to RCB
Goes to RCB to charge battery / run 12V systems
TSAL OUTPUT Pin 13 and 21
Board Function: - CAN IN/OUT from RCB to DCB and Pack 1 - Vicor DC/DC - TSMP - BMS Current - STM32 (Precharge) - TSAL - IMD
Power Resistors
Vicor temperature sensor
EMUS Current Sensor from BMS
CAN Goes to Pack 1 and Dash
Global nets connected to this sheet: GND
HV Danger!
BMS supplies own power to Current Sensor


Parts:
C1: 4.7u; C_0603_1608Metric_Pad1.08x0.95mm_HandSolder
C3, C7, C10, C13, C15, C16, C17: 0.1u; C_0603_1608Metric_Pad1.08x0.95mm_HandSolder
C9: .1u; C_0603_1608Metric_Pad1.08x0.95mm_HandSolder
C12: 10u; C_0603_1608Metric_Pad1.08x0.95mm_HandSolder
D2: LED; LED_0603_1608Metric_Pad1.05x0.95mm_HandSolder
D3: SP0502BAHT; SOT-23
J10: FTSH-107-01-F-DV-k; PinHeader_2x07_P1.27mm_Vertical_SMD
J12: Conn_01x02; JST_XH_B2B-XH-A_1x02_P2.50mm_Vertical
JP1: SolderJumper_2_Bridged; SolderJumper-2_P1.3mm_Bridged_RoundedPad1.0x1.5mm
Q3: DMN3404L; SOT-23_Handsoldering
R7: 330; R_0603_1608Metric_Pad0.98x0.95mm_HandSolder
R11: 100; R_0603_1608Metric_Pad0.98x0.95mm_HandSolder
R12: 10k; R_0603_1608Metric_Pad0.98x0.95mm_HandSolder
R13: 120; R_0603_1608Metric_Pad0.98x0.95mm_HandSolder
U1: MAX33054EASA+T; SOIC127P600X175-8N
U4: LD1117S33TR_SOT223; SOT-223-3_TabPin2
U5: STM32F413CGUx; QFN-48-1EP_7x7mm_P0.5mm_EP5.3x5.3mm
Y1: CSTME8M00; Resonator_SMD_muRata_CSTxExxV-3Pin_3.0x1.1mm_HandSoldering

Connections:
+3V3: C1.1, C3.1, C7.1, C12.1, C13.2, C15.1, C16.1, C17.1, J10.3, R7.2, U1.3 (VDD), U1.5 (VL), U4.2 (VO), U5.9 (VDDA), U5.24 (VDD), U5.36 (VDD), U5.48 (VDD); also elsewhere on the board
+12V: C9.1, J12.2, U4.3 (VI); also elsewhere on the board
/CAN+: D3.2 (K), R13.1, U1.7 (CANH); also elsewhere on the board
/CAN-: D3.1 (K), R13.2, U1.6 (CANL); also elsewhere on the board
/DC_DC_EN: U5.11 (PA1); also elsewhere on the board
/DC_DC_FAULT: U5.12 (PA2); also elsewhere on the board
/TEMP-: R12.2, U5.17 (PA7); also elsewhere on the board
/controller/CAN_RX: U1.4 (RXD), U5.32 (PA11)
/controller/CAN_TX: U1.1 (TXD), U5.33 (PA12)
/controller/FAN_SIG: Q3.1 (G), U5.10 (PA0)
A13_SWDIO: J10.4, U5.34 (PA13)
A14_SWCLK: J10.6, U5.37 (PA14)
B3_TRACESWO: J10.8, U5.39 (PB3)
GND: C3.2, C7.2, C9.2, C10.1, C12.2, C13.1, C15.2, C16.2, C17.2, D2.1 (K), D3.3 (A), J10.5, J10.7, JP1.1 (A), Q3.2 (S), R11.1, R12.1, U1.2 (GND), U1.8 (STBY), U4.1 (GND), U5.8 (VSSA), U5.23 (VSS), U5.35 (VSS), U5.47 (VSS), U5.49 (VSS), Y1.2; also elsewhere on the board
unnamed: C1.2, U5.22 (VCAP_1)
unnamed: C10.2, U5.7 (NRST)
unnamed: D2.2 (A), R7.1
unnamed: J10.11, R11.2
unnamed: J12.1, Q3.3 (D)
unnamed: JP1.2 (B), U5.44 (BOOT0)
unnamed: U5.5 (PH0), Y1.3
unnamed: U5.6 (PH1), Y1.1

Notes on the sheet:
G.Spearing February 2022
Fan Control
PROGRAMMING
Thermistor Input
Power Caps
Power Regulation


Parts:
C2, C19: 0.68uF; C_Rect_L18.0mm_W8.0mm_P15.00mm_FKS3_FKP3
C22, C23: 4700uF; C_Radial_D18.0mm_H35.5mm_P7.50mm
L1: 1uH; L_1008_2520Metric_Pad1.43x2.20mm_HandSolder
L2: 0.15uH; L_0805_2012Metric_Pad1.15x1.40mm_HandSolder
R8: 300; R_0603_1608Metric_Pad0.98x0.95mm_HandSolder
R15, R20: 1; R_2512_6332Metric_Pad1.40x3.35mm_HandSolder
R17, R18: 1k; R_0603_1608Metric_Pad0.98x0.95mm_HandSolder
R19: 10k; R_0603_1608Metric_Pad0.98x0.95mm_HandSolder
RV1: 50k TC33x-2-503E; Potentiometer_Bourns_TC33X_Vertical
U7: Vicor_AERO; vicor-socket-no-cutouts
U8: LTV-817S; SMDIP-4_W9.53mm_Clearance8mm
U9: TLP184; MFSOP6-4_4.4x3.6mm_P1.27mm

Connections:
+3V3: R19.2; also elsewhere on the board
/DCDC_OUT: C23.1, L2.2, R20.1; also elsewhere on the board
/DC_DC_EN: R18.1; also elsewhere on the board
/DC_DC_FAULT: R19.1, U9.6; also elsewhere on the board
/vicor/EN_HV: U7.3 (EN), U8.4
/vicor/FAULT_HV: R17.2, U7.4 (FT)
/vicor/HV+: L1.1, R15.2; also elsewhere on the board
/vicor/TRIM_HV: R8.1, U7.2 (TR)
GND: C22.2, C23.2, U7.8 (-OUT), U8.2, U9.4; also elsewhere on the board
HV-: C2.2, C19.2, RV1.1, U7.5 (-IN), U8.3, U9.3; also elsewhere on the board
unnamed: C2.1, C19.1, L1.2, R15.1, U7.1 (+IN)
unnamed: C22.1, L2.1, R20.2, U7.9 (+OUT)
unnamed: R8.2, RV1.2
unnamed: R17.1, U9.1
unnamed: R18.2, U8.1

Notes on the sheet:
Output Filtering
500V-rated caps
Willem Hillier UVM AERO 3/5/2019
Input Filtering
Trim Control
HV-Interface
Pull high to disable
HV->12V DC-DC
HV Side is pulled high enternally, optoisolator turns on (with high signal) to pull en_hv low
HV Danger!
FAULT_HV can only supply 4mA absolute max, hence the different optocoupler choice.


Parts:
C4, C5: 0.1u; C_0603_1608Metric_Pad1.08x0.95mm_HandSolder
C6: 1u; C_0603_1608Metric_Pad1.08x0.95mm_HandSolder
Q1, Q2: PSMN5R2-60YL; LFPAK56
R1: 39k; R_Axial_DIN0411_L9.9mm_D3.6mm_P25.40mm_Horizontal
R2, R5: 10k; R_0603_1608Metric_Pad0.98x0.95mm_HandSolder
R3: 100k; R_0603_1608Metric_Pad0.98x0.95mm_HandSolder
R4: 235k; R_0603_1608Metric_Pad0.98x0.95mm_HandSolder
R6: 0.75; R_2512_6332Metric_Pad1.40x3.35mm_HandSolder
U2: LTV-817S; SMDIP-4_W9.53mm_Clearance8mm
U3: LM555xM; SOIC-8_3.9x4.9mm_P1.27mm

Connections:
+12V: U2.4; also elsewhere on the board
/TSAL/555_OUT: R5.2, U3.3 (Q)
/TSAL/HV+: R1.2; also elsewhere on the board
/TSAL/pass: C6.1, R4.2, U3.2 (TR), U3.6 (THR)
/TSAL_GND: Q2.5 (D); also elsewhere on the board
GND: C4.2, C5.2, C6.2, Q1.1 (S), Q1.2 (S), Q1.3 (S), R2.2, R6.1, U3.1 (GND); also elsewhere on the board
HV-: U2.2; also elsewhere on the board
unnamed: C4.1, U3.5 (CV)
unnamed: Q1.4 (G), Q2.1 (S), Q2.2 (S), Q2.3 (S), R6.2
unnamed: Q1.5 (D), Q2.4 (G), R5.1
unnamed: R1.1, U2.1
unnamed: R3.2, R4.1, U3.7 (DIS)
VCC: C5.1, R2.1, R3.1, U2.3, U3.4 (R), U3.8 (VCC)

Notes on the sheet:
Change R6 for Current Rating
CC Output
LED Connector
High Voltage



Board: 2 copper layers, 181.6 x 106.0 mm, 71 parts (12 on the bottom side), 51 nets.

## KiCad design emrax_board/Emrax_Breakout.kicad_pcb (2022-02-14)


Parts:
J1: Conn_01x08; TE_1-776280-1_8pin_Horizontal
J2: Conn_01x06; JST_XH_S6B-XH-A-1_1x06_P2.50mm_Horizontal
J3: Conn_01x02; JST_XH_S2B-XH-A-1_1x02_P2.50mm_Horizontal
R1: R; R_0603_1608Metric_Pad0.98x0.95mm_HandSolder

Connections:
+5V: J1.7, R1.1
/COS+: J1.2, J2.3
/COS-: J1.4, J2.4
/EXT+: J1.1, J2.5
/EXT-: J1.6, J2.6
/SIN+: J1.3, J2.1
/SIN-: J1.5, J2.2
/TEMP+: J3.2, R1.2
/TEMP-: J1.8, J3.1

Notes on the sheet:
ampseal


Board: 2 copper layers, 30.4 x 40.9 mm, 4 parts (0 on the bottom side), 9 nets.

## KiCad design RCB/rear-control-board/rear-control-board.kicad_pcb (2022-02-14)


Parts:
C1: .1u; C_0603_1608Metric_Pad1.08x0.95mm_HandSolder
C6: 10u; C_0603_1608Metric_Pad1.08x0.95mm_HandSolder
D1: LED; LED_0603_1608Metric_Pad1.05x0.95mm_HandSolder
H1, H2: MountingHole; MountingHole_3.2mm_M3
J1, J2: Conn_01x23; TE_1-770669-1_23pin_Horizontal
J3: Conn_01x08; TE_1-776280-1_8pin_Horizontal
K1: T9VV1K15-12S; RELAY_T9VV1K15-12S
R2: 330; R_0603_1608Metric_Pad0.98x0.95mm_HandSolder
U3: LDL1117S33R; SOT-223-3_TabPin2

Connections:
+3V3: C6.1, J2.18, J2.19, J2.20, J2.21, J2.22, J2.23, R2.2, U3.2 (VO); also elsewhere on the board
+12V: K1.4; also elsewhere on the board
/BATT_12V: J1.5, J1.6, J1.12, J1.13, K1.3; also elsewhere on the board
/BRAKE_CTRL_12V: J1.4; also elsewhere on the board
/BRB_RTN: J1.20; also elsewhere on the board
/CAN_N: J3.2, J3.4, J3.6; also elsewhere on the board
/CAN_P: J3.3, J3.5, J3.7; also elsewhere on the board
/DCDC_IN: J1.7, J1.8, J1.14, J1.15; also elsewhere on the board
/FAN_CTRL_12V: J1.3; also elsewhere on the board
/FAULT_BMS: J1.22; also elsewhere on the board
/FAULT_IMD: J1.21; also elsewhere on the board
/FuseBank/BRB_LOOP: J1.17; also elsewhere on the board
/FuseBank/FRONT_12V: J1.16; also elsewhere on the board
/FuseBank/RINE_12V: J1.9; also elsewhere on the board
/FuseBank/SPARE_12V: J1.1; also elsewhere on the board
/FuseBank/TSV: J1.23; also elsewhere on the board
/PUMP_CTRL_12V: J1.2; also elsewhere on the board
/REAR_12V: J3.1; also elsewhere on the board
/SSOK: K1.1; also elsewhere on the board
/SUSPENSION_L: J2.14; also elsewhere on the board
/SUSPENSION_R: J2.7; also elsewhere on the board
/WATER_IN-: J2.15; also elsewhere on the board
/WATER_OUT-: J2.8; also elsewhere on the board
/WHEEL_L: J2.13; also elsewhere on the board
/WHEEL_R: J2.6; also elsewhere on the board
GND: C1.2, C6.2, D1.1 (K), J1.10, J1.11, J1.18, J1.19, J2.1, J2.2, J2.9, J2.10, J2.16, J2.17, J3.8, K1.2, U3.1 (GND); also elsewhere on the board
INT_12V: C1.1, U3.3 (VI); also elsewhere on the board
unnamed: D1.2 (A), R2.1

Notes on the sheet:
Once faults are clear relay closes and SSOK lights are on
1.0
Comes from HVB and BMS directly
Global Nets Connected: GND
Main Relay for all car systems Has to be rated up to 40A
checkout parts for temperature monitoring Look for NTC
Global Nets Connected: GND, INT_12V
Voltages for Sensors: Wheel: 2.7 < 24 (voltage ouput) Suspension: 3 < 30V (ratiometric) Steering: 12 < 36 (non-ratiometric, 0-5v output) Brake: <5 (ratiometric)
DON'T FORGET INLINE FUSE FOR BATT_12V
01/20/2022 | 22.020 | G.Spearing
CAN and 12V HVB power
Rear Control Board Functions: CAN, Wheel Speed, Dampers, Fan, Pump, Brake, Main Power Fuses, BRB I/O - CAN from rinehart to HVB CAN is temrinated on Rineart (start of line) End of line is the Pacman Side 2
Goes to FET Control for Switching
To Other Connector
CAN comes from Rinehart goes to HVB
For Shielding
Power Regulation
Global Nets Connected: GND, INT_12V, 3.3v
Sensors are all 3.3V compatable, so powering off that
Global Nets Connected: 12V, INT_12V
Rear Control Board

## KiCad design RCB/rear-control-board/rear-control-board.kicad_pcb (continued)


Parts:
C4: 4.7u; C_0603_1608Metric_Pad1.08x0.95mm_HandSolder
C5, C7, C8, C9, C10, C11, C12: 0.1u; C_0603_1608Metric_Pad1.08x0.95mm_HandSolder
D6, D7, D8: SP0502BAHT; SOT-23
D9: DESD2CAN2SOQ-7; SOT-23
J6: FTSH-107-01-F-DV-K; PinHeader_2x07_P1.27mm_Vertical_SMD
JP1: SolderJumper_2_Bridged; SolderJumper-2_P1.3mm_Bridged_Pad1.0x1.5mm
R4, R7: 1k; R_0603_1608Metric_Pad0.98x0.95mm_HandSolder
R6: 120; R_0603_1608Metric_Pad0.98x0.95mm_HandSolder
R10: 100; R_0603_1608Metric_Pad0.98x0.95mm_HandSolder
U1: STM32F413CGUx; QFN-48-1EP_7x7mm_P0.5mm_EP5.6x5.6mm
U4: MAX33054EASA+T; SOIC127P600X175-8N
Y1: CSTNE8M00; Resonator_SMD_muRata_CSTxExxV-3Pin_3.0x1.1mm_HandSoldering

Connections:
+3V3: C4.2, C7.1, C8.1, C9.1, C10.1, C11.1, C12.1, J6.3, U1.9 (VDDA), U1.24 (VDD), U1.36 (VDD), U1.48 (VDD), U4.3 (VDD), U4.5 (VL); also elsewhere on the board
/CAN_N: D9.1 (K), R6.2, U4.6 (CANL); also elsewhere on the board
/CAN_P: D9.2 (K), R6.1, U4.7 (CANH); also elsewhere on the board
/Controller/BRAKE_CTRL: U1.20 (PB2); also elsewhere on the board
/Controller/CAN_RX: U1.32 (PA11), U4.4 (RXD)
/Controller/CAN_TX: U1.33 (PA12), U4.1 (TXD)
/Controller/FAN_CTRL: U1.19 (PB1); also elsewhere on the board
/Controller/FAULT_IMD: D6.2 (K), U1.16 (PA6); also elsewhere on the board
/Controller/PUMP_CTRL: U1.18 (PB0); also elsewhere on the board
/FAULT_LATCHER/BMS_SWITCH: D6.1 (K), U1.17 (PA7); also elsewhere on the board
/SUSPENSION_L: D7.2 (K), U1.12 (PA2); also elsewhere on the board
/SUSPENSION_R: D7.1 (K), U1.13 (PA3); also elsewhere on the board
/WATER_IN-: R7.1, U1.14 (PA4); also elsewhere on the board
/WATER_OUT-: R4.1, U1.15 (PA5); also elsewhere on the board
/WHEEL_L: D8.2 (K), U1.10 (PA0); also elsewhere on the board
/WHEEL_R: D8.1 (K), U1.11 (PA1); also elsewhere on the board
A13_SWDIO: J6.4, U1.34 (PA13)
A14_SWCLK: J6.6, U1.37 (PA14)
B3_TRACESWO: J6.8, U1.39 (PB3)
GND: C5.2, C7.2, C8.2, C9.2, C10.2, C11.2, C12.2, D6.3 (A), D7.3 (A), D8.3 (A), D9.3 (A), J6.5, J6.7, JP1.1 (A), R4.2, R7.2, R10.1, U1.8 (VSSA), U1.23 (VSS), U1.35 (VSS), U1.47 (VSS), U1.49 (VSS), U4.2 (GND), U4.8 (STBY), Y1.2; also elsewhere on the board
unnamed: C4.1, U1.22 (VCAP_1)
unnamed: C5.1, U1.7 (NRST)
unnamed: J6.11, R10.2
unnamed: JP1.2 (B), U1.44 (BOOT0)
unnamed: U1.5 (PH0), Y1.1
unnamed: U1.6 (PH1), Y1.3

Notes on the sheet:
Water Temperature
check pull down value with ntc 1k works well with a 10k ntc thermistor
CAN Transceiver
add NC pins
Normally a switch is on NRST to reset, but we're ignoring that and will manually reset if necessary
IMD is pulled low, high when clear BMS is pulled high, low when clear
voltage ouput max of sensors are 3.3V
Connectors
Power Caps Place as close as possible to the VDD pins
STBY logic low is normal mode logic high is receive only
PROGRAMMING


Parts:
D3: D_KAK; TO-252-2
F11: 20A; Fuseholder_Blade_Mini_Keystone_3568

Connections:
/BATT_12V: D3.1 (K), D3.3 (K); also elsewhere on the board
/DCDC_IN: F11.2; also elsewhere on the board
/charge-controller/dcdc_fuse: D3.2 (A), F11.1

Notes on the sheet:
Add some currnet protection - Charge controller ic for protection
Not really a charge controller, just a fuse and diode Crude, but functional implementation
INA series chip to mointor current for VICOR. this is if we wanted to do MCU


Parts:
C2, C3, C13: 1u; C_0603_1608Metric_Pad1.08x0.95mm_HandSolder
R1, R14, R16: 20k; R_0603_1608Metric_Pad0.98x0.95mm_HandSolder
R9, R15: 50k; R_0603_1608Metric_Pad0.98x0.95mm_HandSolder
R11, R12, R13: 1.5K; R_0603_1608Metric_Pad0.98x0.95mm_HandSolder
R17: 200k; R_0603_1608Metric_Pad0.98x0.95mm_HandSolder
U5, U6, U7: BV1HAL45EFJ; HTSOP-8-1EP_3.9x4.9mm_P1.27mm_EP2.4x3.2mm_ThermalVias

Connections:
/BRAKE_12V: C13.1, U7.9 (VIN); also elsewhere on the board
/BRAKE_CTRL_12V: U7.7 (OUT), U7.8 (OUT); also elsewhere on the board
/Controller/BRAKE_CTRL: R13.1; also elsewhere on the board
/Controller/FAN_CTRL: R11.1; also elsewhere on the board
/Controller/PUMP_CTRL: R12.1; also elsewhere on the board
/FAN_12V: C2.1, U5.9 (VIN); also elsewhere on the board
/FAN_CTRL_12V: U5.7 (OUT), U5.8 (OUT); also elsewhere on the board
/PUMP_12V: C3.1, U6.9 (VIN); also elsewhere on the board
/PUMP_CTRL_12V: U6.7 (OUT), U6.8 (OUT); also elsewhere on the board
GND: C2.2, C3.2, C13.2, R1.1, R9.1, R14.1, R15.1, R16.1, R17.1, U5.3 (GND), U5.6 (N.C.), U6.3 (GND), U6.6 (N.C.), U7.3 (GND), U7.6 (N.C.); also elsewhere on the board
unnamed: R11.2, U5.5 (EN)
unnamed: R13.2, U7.5 (EN)
unnamed: R1.2, U5.1 (SS)
unnamed: R9.2, U5.2 (ILIM)
unnamed: R14.2, U6.1 (SS)
unnamed: R15.2, U6.2 (ILIM)
unnamed: R12.2, U6.5 (EN)
unnamed: R16.2, U7.1 (SS)
unnamed: R17.2, U7.2 (ILIM)

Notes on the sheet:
2.2mA current limiting resistor


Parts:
D4, D5: 1N4148; D_SOD-123
J4, J5: JST-B2B-VERT-2PIN; JST_XH_B2B-XH-AM_1x02_P2.50mm_Vertical
K2, K3: G5V-2; Relay_DPDT_Omron_G5V-2
R3: 10k; R_0603_1608Metric_Pad0.98x0.95mm_HandSolder
R5: 10K; R_0603_1608Metric_Pad0.98x0.95mm_HandSolder
R8: 2.2K; R_0603_1608Metric_Pad0.98x0.95mm_HandSolder

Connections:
+3V3: R3.1; also elsewhere on the board
/BRB_RTN: K2.9; also elsewhere on the board
/Controller/FAULT_IMD: R5.2, R8.1; also elsewhere on the board
/FAULT_BMS: K2.4; also elsewhere on the board
/FAULT_IMD: K3.4; also elsewhere on the board
/FAULT_LATCHER/BMS_SWITCH: D4.2 (A), J4.1, K2.1, K2.8, R3.2; also elsewhere on the board
/FAULT_LATCHER/IMD_SWITCH: D5.1 (K), J5.2, K3.1, K3.8, R5.1
/SSOK: K3.13; also elsewhere on the board
GND: D5.2 (A), J4.2, K3.16, R8.2; also elsewhere on the board
INT_12V: D4.1 (K), J5.1, K2.16; also elsewhere on the board
unnamed: K2.13, K3.9

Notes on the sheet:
Pulled High, Low when no Fault
IMD IMD_FAULT_SIG is HIGH Clear, LOW Fault IMD_IND is LOW when clear, pulled HIGH when fault
Pulled Low, High when no fault
BMS BMS_FAULT_SIG is LOW Clear, HIGH Fault BMS_IND is HIGH when clear, pulled low when fault


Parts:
F1, F4, F5, F8, F10: 2A; Fuseholder_Blade_Mini_Keystone_3568
F2: 10A; Fuseholder_Blade_Mini_Keystone_3568
F3, F6: 15A; Fuseholder_Blade_Mini_Keystone_3568
F7: 5A; Fuseholder_Blade_Mini_Keystone_3568
F9: 1A; Fuseholder_Blade_Mini_Keystone_3568

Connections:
+12V: F1.1, F2.1, F3.1, F4.1, F5.1, F6.1, F7.1, F8.1, F9.1; also elsewhere on the board
/BRAKE_12V: F8.2; also elsewhere on the board
/FAN_12V: F2.2; also elsewhere on the board
/FuseBank/BRB_LOOP: F9.2; also elsewhere on the board
/FuseBank/FRONT_12V: F4.2; also elsewhere on the board
/FuseBank/RINE_12V: F3.2; also elsewhere on the board
/FuseBank/SPARE_12V: F7.2; also elsewhere on the board
/FuseBank/TSV: F10.2; also elsewhere on the board
/PUMP_12V: F6.2; also elsewhere on the board
/REAR_12V: F5.2; also elsewhere on the board
/SSOK: F10.1; also elsewhere on the board
INT_12V: F1.2; also elsewhere on the board

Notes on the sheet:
SSOK is after fault latcher is clear. Then it goes out to SSOK lights, TSVMS and the CockPit BRB -> which then goes to the Pack AIRs to close the interlock
INT_12V goes to the onboard 5v and 3.3v regulator



Board: 2 copper layers, 99.7 x 113.0 mm, 68 parts (14 on the bottom side), 59 nets.

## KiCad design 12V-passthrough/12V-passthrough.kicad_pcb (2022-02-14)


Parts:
H1, H2, H3, H4, H5, H6: MountingHole_Pad; MountingHole_2.2mm_M2_ISO14580_Pad_TopBottom

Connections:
+12V: H1.1, H2.1, H3.1
GND: H4.1, H5.1, H6.1


Board: 2 copper layers, 14.5 x 9.9 mm, 6 parts (0 on the bottom side), 2 nets.

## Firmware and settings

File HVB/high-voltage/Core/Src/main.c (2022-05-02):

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
/* Includes ------------------------------------------------------------------*/
#include "main.h"

/* USER CODE BEGIN PD */

// analog buffer
#define ADC_BUF_LEN 4086

// precharge
#define PRECHARGE_COEFFICIENT       0.95          // 95% complete with precharge so it's probably safe to continue
#define NUM_COMMAND_MSG             10            // number of command messages we see from rinehart
#define NUM_VOLTAGE_CHECKS          500           // since we're checking at 10ms Interrupts, 500 would be 5 seconds. 
                                                  // precharge should be done in less than 2 seconds. 
/* USER CODE END PD */

ADC_HandleTypeDef hadc1;
DMA_HandleTypeDef hdma_adc1;

CAN_HandleTypeDef hcan1;

TIM_HandleTypeDef htim13;
TIM_HandleTypeDef htim14;

/* USER CODE BEGIN PV */

// counters for Rinehart message sending in precharge
uint8_t rinehart_send_command_count = 0;

// inputs
uint32_t rinehartVoltage = 0;                 // read from CAN
uint32_t bmsVoltage = 0;					            // read from CAN
int vicoreTemp = 0;					                  // read from DMA, vicore temp
int DCDCEnable = 0;                           // dc-dc enable (0 = disabled, 1 = enabled)
int RTDButtonPressed = 0;                     // read this from CAN, if it's 1 we can finish precharge
uint32_t adc_buf[ADC_BUF_LEN];				        // adc read buffer

// output
int DCDCFault = 0;                            // the dc-dc fault indicator (0 = no fault, 1 = fault)
int readyToDrive = 0;					                // the car is ready to drive! (0 = not ready, 1 = ready)

// precharge states
enum prechargeStates
{
	PRECHARGE_OFF,
	PRECHARGE_ON,
	PRECHARGE_DONE,
	PRECHARGE_ERROR
};
uint8_t prechargeState = PRECHARGE_OFF;			  // set initial precharge state to OFF
uint8_t lastPrechargeState = PRECHARGE_OFF;
uint8_t voltageCheckCount = 0;

// CAN transmit 
uint32_t TxMailbox; 							            // CAN Bus Mail box variable
CAN_TxHeaderTypeDef txHeader0; 					      // CAN Bus Transmit Header BASE
CAN_TxHeaderTypeDef txHeader1; 					      // CAN Bus Transmit Header DATA
CAN_TxHeaderTypeDef txHeader2; 					      // CAN Bus Transmit Header DATA
uint8_t TxData[8];                            // CAN transmit buffer

// CAN recive
CAN_RxHeaderTypeDef rxHeader; 					      // CAN Bus Receive Header
uint8_t canRX[8] = {0, 0, 0, 0, 0, 0, 0, 0}; 	// CAN Bus Receive Buffer

CAN_FilterTypeDef canFilter0; 					      // CAN Bus Filter for BMS
CAN_FilterTypeDef canFilter1;                 // CAN Bus Filter for Rinehart
/* USER CODE END PV */

void SystemClock_Config(void);
static void MX_GPIO_Init(void);
static void MX_CAN1_Init(void);
static void MX_DMA_Init(void);
static void MX_ADC1_Init(void);
static void MX_TIM14_Init(void);
static void MX_TIM13_Init(void);
/* USER CODE BEGIN PFP */
void prechargeControl();

/* USER CODE END PFP */

/**
  * @brief  The application entry point.
  * @retval int
  */
int main(void)
{
  /* MCU Configuration--------------------------------------------------------*/

  /* Reset of all peripherals, Initializes the Flash interface and the Systick. */
  HAL_Init();

  /* Configure the system clock */
  SystemClock_Config();

  /* Initialize all configured peripherals */
  MX_GPIO_Init();
  MX_CAN1_Init();
  MX_DMA_Init();
  MX_ADC1_Init();
  MX_TIM14_Init();
  MX_TIM13_Init();
  /* USER CODE BEGIN 2 */

  // init the CAN mailbox for BASE
  txHeader0.DLC = 8; // Number of bites to be transmitted max- 8
  txHeader0.IDE = CAN_ID_STD;
  txHeader0.RTR = CAN_RTR_DATA;
  txHeader0.StdId = 0x086;
  txHeader0.ExtId = 0;
  txHeader0.TransmitGlobalTime = DISABLE;

  // init the CAN mailbox for DATA
  txHeader1.DLC = 8; // Number of bites to be transmitted max- 8
  txHeader1.IDE = CAN_ID_STD;
  txHeader1.RTR = CAN_RTR_DATA;
  txHeader1.StdId = 0x087;
  txHeader1.ExtId = 0;
  txHeader1.TransmitGlobalTime = DISABLE;

  // header for rinehart (Parameter Command Message)
  txHeader2.DLC = 8; // Number of bites to be transmitted max- 8
  txHeader2.IDE = CAN_ID_STD;
  txHeader2.RTR = CAN_RTR_DATA;
  txHeader2.StdId = 0x0C1;
  txHeader2.ExtId = 0;
  txHeader2.TransmitGlobalTime = DISABLE;

	HAL_CAN_Start(&hcan1); // Initialize CAN Bus
	HAL_CAN_ActivateNotification(&hcan1, CAN_IT_RX_FIFO0_MSG_PENDING);   // Initialize CAN Bus Rx Interrupt

  // start timers
  HAL_TIM_Base_Start_IT(&htim14);
  HAL_TIM_Base_Start_IT(&htim13);

	// start ADC DMA
	HAL_ADC_Start_DMA(&hadc1, adc_buf, ADC_BUF_LEN);

  /* USER CODE END 2 */

  /* Infinite loop */
  /* USER CODE BEGIN WHILE */
  while (1)
  {
    /* USER CODE END WHILE */

    /* USER CODE BEGIN 3 */
  }
  /* USER CODE END 3 */
}

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
/* USER CODE BEGIN 4 */

// *** functions *** //


/**
 * overwriting the weak function defined in the includes which is the ISR for the CAN interrupt
 */
void HAL_CAN_RxFifo0MsgPendingCallback(CAN_HandleTypeDef *hcan1)
{
  if (HAL_CAN_GetRxMessage(hcan1, CAN_RX_FIFO0, &rxHeader, canRX) != HAL_OK)
    Error_Handler();

  // get rinehart bus voltage
  if (rxHeader.StdId == 0x0A7 && rxHeader.DLC == 8)    // sometimes rinehart sends 0 length messages so only read when there's data
  {
    // rinehart voltage is spread across the first 2 bytes
	  int rine1 = canRX[0];
    int rine2 = canRX[1];

    // combine the first two bytes and assign that to the rinehart voltage
    rinehartVoltage = (rine2 << 8) | rine1;
  }

  // get BMS total voltages
  if (rxHeader.StdId == 0x6B0)
  {
    // BMS voltage is spread across the first 2 bytes
	  int volt1 = canRX[2];
    int volt2 = canRX[3];

    // combine the first two bytes and assign that to the BMS voltage
    bmsVoltage = (volt1 << 8) | volt2; // orion has a pre-scaller of *10
  }
}


/**
 * @brief 
 * 
 */
void prechargeControl()
{
  // NOTE: Weird thing about Rinehart 0x0A7 message: 
  //      Sometimes it sends a 0 byte length data. Make sure we're only reading
  //      The value if the DLC is 8
	switch (prechargeState)
	{
		case (PRECHARGE_OFF):
			// set ready to drive to false
			readyToDrive = 0;

      // this state sends a message to rinehart
      // if (lastPrechargeState != prechargeState)
      // {
        // message is sent to rinehart to turn everything off
        TxData[0] = 1;          // parameter address. LSB
        TxData[1] = 0;          // parameter address. MSB
        TxData[2] = 1;          // Read / Write. 1 is write
        TxData[3] = 0;          // N/A
        TxData[4] = 0;          // Data. "0" off, "1": relay 1 on, "2": relay 2 on, "3": relay 1 and 2 on
        TxData[5] = 0x55;         // 55 means relay control
        TxData[6] = 0;          // N/A
        TxData[7] = 0;          // N/A

        // send message
        HAL_CAN_AddTxMessage(&hcan1, &txHeader2, TxData, &TxMailbox);
        
        // update last precharge state
        // lastPrechargeState = prechargeState;
      // }

      // move to precharge on
      prechargeState = PRECHARGE_ON;
		break;

		case (PRECHARGE_ON):
      // not ready to drive yet
      readyToDrive = 0;

      // turn on precharge relay
      // this state sends a message to rinehart to turn 
      // if (lastPrechargeState != prechargeState)
      // {
        // message is sent to rinehart to turn on precharge relay
        // precharge relay is on relay 1 from Rinehart
        TxData[0] = 1;            // parameter address. LSB
        TxData[1] = 0;            // parameter address. MSB
        TxData[2] = 1;            // Read / Write. 1 is write
        TxData[3] = 0;            // N/A
        TxData[4] = 1;            // Data. "0" off, "1": relay 1 on, "2": relay 2 on, "3": relay 1 and 2 on
        TxData[5] = 0x55;           // 55 means relay control
        TxData[6] = 0;            // N/A
        TxData[7] = 0;            // N/A

        // send message
        HAL_CAN_AddTxMessage(&hcan1, &txHeader2, TxData, &TxMailbox);
        
        // update last precharge state
        // lastPrechargeState = prechargeState;
      // }
      
			// ensure voltages are above correct values
			if ((rinehartVoltage > (bmsVoltage * PRECHARGE_COEFFICIENT)) && (bmsVoltage > 220))   // 220 so not just 1 pack can trigger this
      {
        prechargeState = PRECHARGE_DONE;
      }

      // if we do this for too long, move to error state
      // if (voltageCheckCount >= NUM_VOLTAGE_CHECKS)
      // {
      //   prechargeState = PRECHARGE_ERROR;
      // }
      
      // else
      // {
      //   voltageCheckCount++; // add to the counter. 
      // }
		break;

		case (PRECHARGE_DONE):
      // this state sends a message to rinehart to turn 
      // if (lastPrechargeState != prechargeState)
      // {
        // message is sent to rinehart to turn everything on
        // Keep precharge relay on and turn on main contactor
        TxData[0] = 1; // parameter address. LSB
        TxData[1] = 0; // parameter address. MSB
        TxData[2] = 1; // Read / Write. 1 is write
        TxData[3] = 0; // N/A
        TxData[4] = 3; // Data. "0" off, "1": relay 1 on, "2": relay 2 on, "3": relay 1 and 2 on
        TxData[5] = 0x55; // 55 means relay control
        TxData[6] = 0; // N/A
        TxData[7] = 0; // N/A

        // send message
        HAL_CAN_AddTxMessage(&hcan1, &txHeader2, TxData, &TxMailbox);

        // now that precharge is complete we can drive the car
        readyToDrive = 1;
          
        // update last precharge state
        // lastPrechargeState = prechargeState;
      // }

      // if rinehart voltage drops below battery, something's wrong, 
      // turn everything off
			// if (rinehartVoltage <= (bmsVoltage * (PRECHARGE_COEFFICIENT)-20)) // 20 is a magic number
      // {
      //   prechargeState = PRECHARGE_OFF; // something weird happened. Go to error
      // }
		break;

		case (PRECHARGE_ERROR):
			// the car is most definitly not ready to drive
      // set ready to drive off 
			readyToDrive = 0;

      // if (lastPrechargeState != prechargeState)
      // {
        // message is sent to rinehart to turn everything off
        TxData[0] = 1;            // parameter address. LSB
        TxData[1] = 0;            // parameter address. MSB
        TxData[2] = 1;            // Read / Write. 1 is write
        TxData[3] = 0;            // N/A
        TxData[4] = 0;            // Data. "0" off, "1": relay 1 on, "2": relay 2 on, "3": relay 1 and 2 on
        TxData[5] = 0x55;           // 55 means relay control
        TxData[6] = 0;            // N/A
        TxData[7] = 0;            // N/A

        // send message
        HAL_CAN_AddTxMessage(&hcan1, &txHeader2, TxData, &TxMailbox);
        
        // update last precharge state
        // lastPrechargeState = prechargeState;
      // }
		break;

		default:
      // fall back state, this indicates we did some undefined action that brought us here
      // we will move to PRECHARGE_ERROR to ensure readyToDrive stays false :)
			prechargeState = PRECHARGE_ERROR;
		break;
	}
}

void HAL_TIM_PeriodElapsedCallback(TIM_HandleTypeDef *htim)
{
  // on __Hz interval
  if (htim == &htim14)
  {
    // build message for _____
    TxData[0] = readyToDrive;               // controled by precharge
    TxData[1] = DCDCFault;                  // 0 for now TODO: implement fault detection
    TxData[2] = vicoreTemp;                 // DMA update
    TxData[3] = rinehartVoltage & 0xFF;     // update on CAN message LSB
    TxData[4] = rinehartVoltage >> 8;       // update on CAN message MSB
    TxData[5] = bmsVoltage & 0xFF;          // update on CAN message LSB
    TxData[6] = bmsVoltage >> 8;            // update on CAN message MSB
    TxData[7] = prechargeState;             // show which state of precharge / driving we're in, 0:off, 1:pre, 2: main

    // send message
    HAL_CAN_AddTxMessage(&hcan1, &txHeader1, TxData, &TxMailbox);
  }

  // on __Hz interval 
  if(htim == &htim13)
  {
    // check precharge status
    prechargeControl();
  }
}

void HAL_ADC_ConvCpltCallback(ADC_HandleTypeDef* hadc)
{
  // TODO: check analog values for the temperature conversion
  // Define threshold for when the fan should turn on

  // update vicor temp
  vicoreTemp = adc_buf[0];

  // set fan based on value
  if (vicoreTemp >= 2048)
  {
    // set the fan high
    HAL_GPIO_WritePin(GPIOA, GPIO_PIN_0, GPIO_PIN_SET);
  }

  else
  {
    // set fan low
    HAL_GPIO_WritePin(GPIOA, GPIO_PIN_0, GPIO_PIN_RESET);
  }
}

/* USER CODE END 4 */
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


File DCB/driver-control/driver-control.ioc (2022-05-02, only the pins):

Mcu.UserName=STM32F413CGUx
PA10.Signal=GPIO_Output
PA11.Signal=CAN1_RX
PA12.Signal=CAN1_TX
PA13.Signal=SYS_JTMS-SWDIO
PA14.Signal=SYS_JTCK-SWCLK
PA4.Signal=ADCx_IN4
PA5.Signal=ADCx_IN5
PA6.Signal=ADCx_IN6
PA7.Signal=ADCx_IN7
PB15.Signal=GPXTI15
PB2.Signal=GPIO_Output
PB8.Signal=GPIO_Output

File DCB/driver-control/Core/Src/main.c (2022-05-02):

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
/* Includes ------------------------------------------------------------------*/
#include "main.h"

/* USER CODE BEGIN PD */
#define ADC_BUF_LEN               4
#define MAX_PEDAL_SKEW            100
#define PEDAL_MAX                 600     // max pedal found from Accelerator test 12bit ADC
#define PEDAL_MIN                 128     // max pedal found from Accelerator test 12bit ADC
#define PEDAL_DEADBAND            10      // max pedal found from Accelerator test 12bit ADC
#define BRAKE_LIGHT_THRESHOLD     10      // when the brake light turns on
#define TORQUE_DEADBAND           5       // commanded torque deadband 
#define MAX_TORQUE                220     // MAX TORQUE RINEHART CAN ACCEPT, DO NOT CHANGE (230)

/* USER CODE END PD */

ADC_HandleTypeDef hadc1;
DMA_HandleTypeDef hdma_adc1;

CAN_HandleTypeDef hcan1;

TIM_HandleTypeDef htim13;
TIM_HandleTypeDef htim14;

/* USER CODE BEGIN PV */

// CAN transmitting
CAN_TxHeaderTypeDef TxHeader;               // either daq or control idk which one address 
CAN_TxHeaderTypeDef TxHeader2;              // rinehart command message address
uint8_t TxData[8];
uint32_t TxMailbox;

// CAN reciving 
CAN_RxHeaderTypeDef RxHeader;
uint8_t RxData[8];
CAN_FilterTypeDef filter0;                  // filter for __________
CAN_FilterTypeDef filter1;                  // fiter for ___________

// signal variables (0 = off | 1 = on)
uint8_t imdFault = 0;             
uint8_t bmsFault = 0;
uint8_t switch_cooling = 0;
uint8_t switch_direction = 0;               // 0 = forward | 1 = reverse (this changes requires an inverter restart)
uint8_t brakeLight = 0;

// analog pins
uint16_t adc_buf[ADC_BUF_LEN];
uint16_t brake0 = 0;
uint16_t brake1 = 0;
uint16_t pedal0 = 0;
uint16_t pedal1 = 1;
uint16_t brakeAverage = 0;
uint16_t pedalAverage = 0;

// state variables (0 = off | 1 = on)
uint8_t ready_to_drive = 0;                 // 0 until precharge is done
uint8_t buzzerState = 0;                    // for controlling the buzzer
uint8_t buzzerCounter = 0;                  // counter for how long the buzzer has been buzzing
uint8_t enableInverter = 0;                 // stores state of inverter, can only be 1 after buzzer is done buzzing 

// rinehart commands
uint16_t commandedTorque = 0;               // torque request sent to rinehart, init with 0 to prevent unintended acceleration 
uint16_t command_torque_limit = 0;          // max torque allowed to be requested from rinehart, init with 0 to prevent unintended accleration
enum mode                                   // create an enumeration for the drive modes
{
  SLOW,       // 50% power 
  ECO,        // 75% power
  FAST        // 100% power 
};
int driveMode = ECO;                        // set the inital drive mode of the car

/* USER CODE END PV */

void SystemClock_Config(void);
static void MX_GPIO_Init(void);
static void MX_CAN1_Init(void);
static void MX_DMA_Init(void);
static void MX_ADC1_Init(void);
static void MX_TIM14_Init(void);
static void MX_TIM13_Init(void);
/* USER CODE BEGIN PFP */
uint16_t adc_average(uint16_t adc0, uint16_t adc1);
long mapValue(long x, long in_min, long in_max, long out_min, long out_max);
uint16_t getCommandedTorque();

/* USER CODE END PFP */

/**
  * @brief  The application entry point.
  * @retval int
  */
int main(void)
{
  /* USER CODE BEGIN 1 */

  // define TX header
  TxHeader.StdId = 0x093;
  TxHeader.ExtId = 0x0;
  TxHeader.IDE = CAN_ID_STD;
  TxHeader.RTR = CAN_RTR_DATA;
  TxHeader.DLC = 8;
  TxHeader.TransmitGlobalTime = DISABLE;
  
  // Rinehart command message
  TxHeader2.StdId = 0x0C0;
  TxHeader2.ExtId = 0x0;
  TxHeader2.IDE = CAN_ID_STD;
  TxHeader2.RTR = CAN_RTR_DATA;
  TxHeader2.DLC = 8;
  TxHeader2.TransmitGlobalTime = DISABLE;

  /* USER CODE END 1 */

  /* MCU Configuration--------------------------------------------------------*/

  /* Reset of all peripherals, Initializes the Flash interface and the Systick. */
  HAL_Init();

  /* Configure the system clock */
  SystemClock_Config();

  /* Initialize all configured peripherals */
  MX_GPIO_Init();
  MX_CAN1_Init();
  MX_DMA_Init();
  MX_ADC1_Init();
  MX_TIM14_Init();
  MX_TIM13_Init();
  /* USER CODE BEGIN 2 */

  // start interrupts
  HAL_CAN_Start(&hcan1);
  HAL_CAN_ActivateNotification(&hcan1, CAN_IT_RX_FIFO0_MSG_PENDING);
  HAL_TIM_Base_Start_IT(&htim14);
  HAL_TIM_Base_Start_IT(&htim13);
  HAL_ADC_Start_DMA(&hadc1, (uint32_t*)adc_buf, ADC_BUF_LEN);

  /* USER CODE END 2 */

  /* Infinite loop */
  /* USER CODE BEGIN WHILE */
  while (1)
  {

    /* USER CODE END WHILE */

    /* USER CODE BEGIN 3 */
  }
  /* USER CODE END 3 */
}

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
/* USER CODE BEGIN 4 */

// re-map function
long mapValue(long x, long in_min, long in_max, long out_min, long out_max) {
  return (x - in_min) * (out_max - out_min) / (in_max - in_min) + out_min;
}


// function to re-map the pedal value to a torque value based on the drive mode
uint16_t getCommandedTorque()
{
  // get the pedal average
  pedalAverage = adc_average(pedal0, pedal1);

  // drive mode logic
  switch (driveMode)
  {
    case SLOW:  // runs at 50% power
      commandedTorque = mapValue(pedalAverage, PEDAL_MIN, PEDAL_MAX, 0, MAX_TORQUE * 0.50);
    break;

    case ECO:   // runs at 75% power
      commandedTorque = mapValue(pedalAverage, PEDAL_MIN, PEDAL_MAX, 0, MAX_TORQUE * 0.75);
    break;

    case FAST:  // runs at 100% power
      commandedTorque = mapValue(pedalAverage, PEDAL_MIN, PEDAL_MAX, 0, MAX_TORQUE);
    break;
    
    // error state, set the mode to ECO
    default:
      // set the state to ECO for next time
      driveMode = ECO;

      // we don't want to send a torque if we are in an undefined state
      commandedTorque = 0;
    break;
  }

  // for throttle safety, we will have a deadband
  if (commandedTorque <= TORQUE_DEADBAND)   // if less than 5% power is requested, just call it 0
  {
    commandedTorque = 0;
  }

  return commandedTorque;
}

// Recive CAN Messages
void HAL_CAN_RxFifo0MsgPendingCallback(CAN_HandleTypeDef *hcan)
{
  if (HAL_CAN_GetRxMessage(&hcan1, CAN_RX_FIFO0, &RxHeader, RxData) != HAL_OK){
    Error_Handler();
  }

  // read CAN data from Rear Control Board
  if (RxHeader.StdId == 0x082)
  {
      imdFault = RxData[0];
      bmsFault = RxData[1];
  }

  // read CAN data from High Voltage Board 
  if (RxHeader.StdId == 0x087)
  {
      ready_to_drive = RxData[0];
  }
}

void HAL_GPIO_EXTI_Callback(uint16_t GPIO_Pin)
{
  // handle start button interrupt
  if (GPIO_Pin == GPIO_PIN_15)
  {
    // if ready to drive & the button has been pushed, start the buzzer
    if (ready_to_drive)
    {
      buzzerState = 1;
    }
  }
}
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

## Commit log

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2021-11-10 initializing board and firmware
    [demo.kicad_pcb, demo.sch, demo_pinout.csv]
2021-11-16 initializing project files
    - create hardware schematic for dev board (with CAN)
    - create CubeIDE project and assign a few pins (empty code)
    [demo.sch]
2021-12-03 removing demo, it's now it's own repo
    [demo.kicad_pcb, demo.sch, demo_pinout.csv]
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2021-12-04 merging the demo board back in
    [demo.kicad_pcb, demo.sch, demo_pinout.csv]
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2022-01-20 creating schematic for RCB
    [Controller.sch, FAULT_LATCHER.sch, FET_OUTPUT.sch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]
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2022-01-22 append HV schematics from old files
    [TSAL.sch, controller.sch, vicor.sch]
2022-01-22 finish schematic, start layout
    [Controller.sch, FET_OUTPUT.sch, charge-controller.sch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]
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2022-01-22 layout and connector pins
    [rear-control-board.kicad_pcb, rear-control-board.sch]
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2022-01-24 updating to new kicad version
    [Controller.kicad_sch, FAULT_LATCHER.kicad_sch, FET_OUTPUT.kicad_sch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]
2022-01-25 working on layout for boards
    HVB and PAM layouts. Also updating files to new kicad version
    [TSAL.kicad_sch, controller.kicad_sch, high-voltage-board.kicad_pcb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]
2022-01-26 working on layout
    Updating traces for RCB and organizing HVB
    [Controller.kicad_sch, FAULT_LATCHER.kicad_sch, FET_OUTPUT.kicad_sch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]
2022-01-26 adding resolver project
    initialized project
    [emrax_resolver.kicad_pcb, emrax_resolver.kicad_sch]
2022-01-26 adding bms pass through board
    initializing BPB project
    [bms_passthrough.kicad_pcb, bms_passthrough.kicad_sch]
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2022-01-29 DCB Layout Rev 1 Complete
    Complete the layout first draft
    [driver-control-board.kicad_sch]
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2022-01-29 almost done with layout
    HV layout almost done. Tracing
    [controller.kicad_sch, high-voltage-board.kicad_pcb, high-voltage-board.kicad_sch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]
2022-01-30 finishing layout placement
    Still need to route wires
    [Controller.kicad_sch, rear-control-board.kicad_pcb, rear-control-board.kicad_sch]
2022-01-30 updating pcb size and layout
    [controller.kicad_sch, high-voltage-board.kicad_sch, vicor.kicad_sch]
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2022-01-30 adding corner cutout and updating layout
    [high-voltage-board.kicad_pcb]
2022-01-30 adjusting pinout, updating layout
    [rear-control-board.kicad_pcb]
2022-01-30 Layout Trace Complete
    completed layout of tracks. Still need to place silkscreens
    [controller.kicad_sch, high-voltage-board.kicad_pcb, high-voltage-board.kicad_sch]
2022-01-30 updating trace correction temp
    changing trace and pinout of a temp wire
    [high-voltage-board.kicad_pcb, high-voltage-board.kicad_sch]
2022-01-30 trace layout complete (need review)
    [Controller.kicad_sch, FAULT_LATCHER.kicad_sch, rear-control-board.kicad_pcb]
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2022-01-31 power filtering and notes
    [Controller.kicad_sch, rear-control-board.kicad_sch]
2022-01-31 updating filtering cap layout
    Kay suggested layout changes. Moved caps around
    [Controller.kicad_sch, controller.kicad_sch, driver-control-board.kicad_pcb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]
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2022-02-01 DRC and Labeling Complete
    [high-voltage-board.kicad_pcb]
2022-02-02 Add files via upload
    emrack pcb
    [Emrax_Breakout.kicad_pcb, Emrax_Breakout.kicad_sch, Emrax_Breakout.sch]
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2022-02-02 put files in folder
    [Emrax_Breakout.kicad_pcb, Emrax_Breakout.kicad_sch, Emrax_Breakout.sch]
2022-02-02 DRC and layout update
    [rear-control-board.kicad_pcb]
2022-02-02 updating emrax board location
    [Emrax_Breakout.kicad_pcb, Emrax_Breakout.kicad_sch, Emrax_Breakout.sch]
2022-02-02 initial emrax board design
    [Emrax_Breakout.kicad_pcb, Emrax_Breakout.kicad_sch, Emrax_Breakout.sch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]
2022-02-02 initial 12V board layout
    [12V-passthrough.kicad_pcb, 12V-passthrough.kicad_sch]
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2022-02-02 initializing pacman side 2 file
    [pacman_side_2.kicad_pcb, pacman_side_2.kicad_sch]
2022-02-02 merging interface board from main
    [interface-board.kicad_pcb, interface-board.kicad_sch]
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2022-02-02 updating side 2 mirror
    [pacman.kicad_pcb, pacman.kicad_sch, pacman_side_2.kicad_pcb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]
2022-02-02 updating footprint and 3d model links
    [high-voltage-board.kicad_pcb, high-voltage-board.kicad_sch, rear-control-board.kicad_pcb]
2022-02-03 finish layout and labeling
    [pacman_side_2.kicad_pcb]
2022-02-03 layout and labeling update
    [pacman.kicad_pcb]
2022-02-03 Layout and Footprints update
    [TSAL.kicad_sch, controller.kicad_sch, high-voltage-board.kicad_pcb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]
2022-02-03 update layout and labeling
    [rear-control-board.kicad_pcb]
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2022-02-03 Update layout with more connectors
    Added passthrough for BMS
    [driver-control-board.kicad_pcb]
2022-02-04 Adding CAN termination resistors
    [pacman.kicad_pcb, pacman.kicad_sch, pacman_side_2.kicad_pcb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]
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2022-02-05 removing old board files
    [Emrax_Breakout.kicad_pcb, Emrax_Breakout.kicad_sch, Emrax_Breakout.sch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]
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2022-02-06 updating board review BOM with notes
    [Combined_Board_BOM.xlsx]
2022-02-06 start to interface with all surface mounted parts
    [interface board smd.kicad_pcb, interface board smd.kicad_sch]
2022-02-06 Major Review and Part Update
    updating footprints, component values, layouts
    [Combined_Board_BOM.xlsx, Controller.kicad_sch, FAULT_LATCHER.kicad_sch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]
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2022-02-14 change schem and finish layout Ready for Review
    [Emrax_Breakout.kicad_pcb, Emrax_Breakout.kicad_sch]
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2022-04-08 formatting & more buzzer logic
    [main.c]
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2022-04-12 start button LED & fixed IMD fault LED bug
    [main.c]
2022-04-12 fixed flipped bit LED bug
    [main.c]
2022-04-13 Revert "fixed flipped bit LED bug"
    This reverts commit 6415d42a2b260cc07f7e59d0e685321f98522efd.
    [main.c]
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2022-04-16 CAN and RTD Buzzer works
    [main.c, rear-control.ioc]
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2022-04-29 fixed dcb can torque message
    [main.c]
2022-04-30 fixed deadband, and simplified some other stuff
    [main.c]
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2022-05-01 fixed torque ranges
2022-05-01 maybe fixed can address issue
    [main.c]
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

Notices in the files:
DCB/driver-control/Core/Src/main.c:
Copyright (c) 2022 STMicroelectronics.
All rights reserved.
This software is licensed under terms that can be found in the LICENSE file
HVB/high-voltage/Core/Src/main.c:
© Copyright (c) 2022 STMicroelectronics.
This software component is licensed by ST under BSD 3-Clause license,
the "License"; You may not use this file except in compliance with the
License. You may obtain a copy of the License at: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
